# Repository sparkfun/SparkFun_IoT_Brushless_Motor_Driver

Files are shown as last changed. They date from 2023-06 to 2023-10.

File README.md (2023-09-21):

SparkFun IoT Brushless Motor Driver (ESP32 WROOM, TMC6300)
========================================

SparkFun IoT Brushless Motor Driver (ESP32 WROOM, TMC6300) (https://www.sparkfun.com/products/22132)

[*SparkFun IoT Brushless Motor Driver (ESP32 WROOM, TMC6300) (ROB-22132)*](https://www.sparkfun.com/products/22132)

The SparkFun IoT Brushless Motor Driver is an all-in-one development platform. It includes all the components to create a simple IoT device or learn about [control systems](https://en.wikipedia.org/wiki/Control_system). On the boaard, users will find an ESP32 microcontroller, a TMC6300 motor driver, a [gimbal motor](https://www.sparkfun.com/products/20441), a TMAG5273 hall-effect sensor, three INA240A1 inline current sensors, an MCP6021T low-side current sensor, two user buttons, a Qwiic connector, a 3-pin JST connector (for the gimbal motor), and a WS2812 RGB LED.

The TMC6300 from [ADI + Trinamic](https://www.trinamic.com/) is a powerful and easy-to-use three-phase motor driver with up to 2A (1.4A<sub>RMS</sub>) of total drive current. Separate high-side and low-side control of the three half-bridges allows for incredible control of each phase of the [motor commutation](https://fab.cba.mit.edu/classes/865.21/topics/power_electronics/commutation/#bldc-commutation). We've found the [*Arduino Simple Field Oriented Control*](https://docs.simplefoc.com/) library to work well with the TMC6300 motor driver.

However, a field-oriented control (FOC) algorithm requires some feedback to close and optimize the control loop. Therefore, we integrated a TMAG5273 hall-effect sensor and INA240A1 current sensor amplifiers *(both manufactured by [Texas Instruments](https://www.ti.com/))* into the design of the IoT motor driver board. This allows users to incorporate a [position sensor](https://docs.simplefoc.com/position_sensors) and [current sensing](https://docs.simplefoc.com/current_sense) into the FOC algorithm or any feedback control loop they choose to implement.

Repository Contents
-------------------

* **[/docs](/docs/)** - Online documentation files
    * [assets](/docs/assets/) - Assets files
        * [arduino_examples](/docs/assets/arduino_examples/) - Example code
        * [board_files](/docs/assets/board_files/) - Files for the product design
            * [Eagle design files](/docs/assets/board_files/eagle_files.zip) (.zip)
            * [Schematic](/docs/assets/board_files/schematic.pdf) (.pdf)
            * [Dimensions](/docs/assets/board_files/dimensions.pdf) (.pdf)
        * [component_documentation](/docs/assets/component_documentation/) - Datasheets for hardware components
        * [img/hookup_guide/](/docs/assets/img/hookup_guide/) - Images for hookup guide documentation
* **[/Hardware](/Hardware/)** - Eagle design files (.brd, .sch)
* **[/Production](/Production/)** - Production files

Documentation
--------------

* **[Hookup Guide (mkdocs)](http://docs.sparkfun.com/SparkFun_IoT_Brushless_Motor_Driver/)** - Hookup guide for the IoT Brushless Motor Driver hosted by GitHub pages.

*Need to download or print our hookup guide?*

* [Print *(Print to PDF)* from Single-Page View](http://docs.sparkfun.com/SparkFun_IoT_Brushless_Motor_Driver/print_view)

Product Variants
----------------

* [ROB-22132](https://www.sparkfun.com/products/22132)- v1.0, Initial Release

Version History
---------------

* [v10](https://github.com/sparkfun/SparkFun_IoT_Brushless_Motor_Driver/releases/tag/v10) - Initial Release

License Information
-------------------

This product is ***open source***!

Please review the [`LICENSE.md`](./LICENSE.md) file for license information.

If you have any questions or concerns about licensing, please contact technical support on our [SparkFun forums](https://forum.sparkfun.com/viewforum.php?f=152).

Distributed as-is; no warranty is given.

- Your friends at SparkFun.

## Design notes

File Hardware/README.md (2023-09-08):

SparkFun IoT Brushless Motor Driver Design Files
=====================================

The .sch and .brd files hare are Eagle CAD schematic and PCB design files from SparkFun Electronics.
A freeware version of Autodesk Eagle can be found [here](https://www.autodesk.com/products/eagle/free-download).

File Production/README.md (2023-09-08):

SparkFun IoT Brushless Motor Driver Production Files
=========================================

These are the production files SparkFun uses for printing PCBs.

License Information
-------------------
This product is open source! 

The hardware is released under [Creative Commons ShareAlike 4.0 International](https://creativecommons.org/licenses/by-sa/4.0/).

Please use, reuse, and modify these files as you see fit. Please maintain attribution to SparkFun Electronics and release anything derivative under the same license.

Distributed as-is; no warranty is given.

- Your friends at SparkFun.

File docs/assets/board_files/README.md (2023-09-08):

board_files directory
====================

1. A `dimensions*.pdf` file containing the board's measurements.
2. A `schematic.pdf` file containing the board's schematics.
3. An `eagle_files*.zip` folder containing the Eagle CAD schematics (`*.sch`) and PCB design (`*.brd`) files.
	* A freeware version of Autodesk Eagle can be found [here](https://www.autodesk.com/products/eagle/free-download).

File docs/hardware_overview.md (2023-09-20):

---
icon: material/cog
---

## Board Dimensions
The board dimensions are illustrated in the drawing below; the listed measurements are in inches.

<figure markdown>
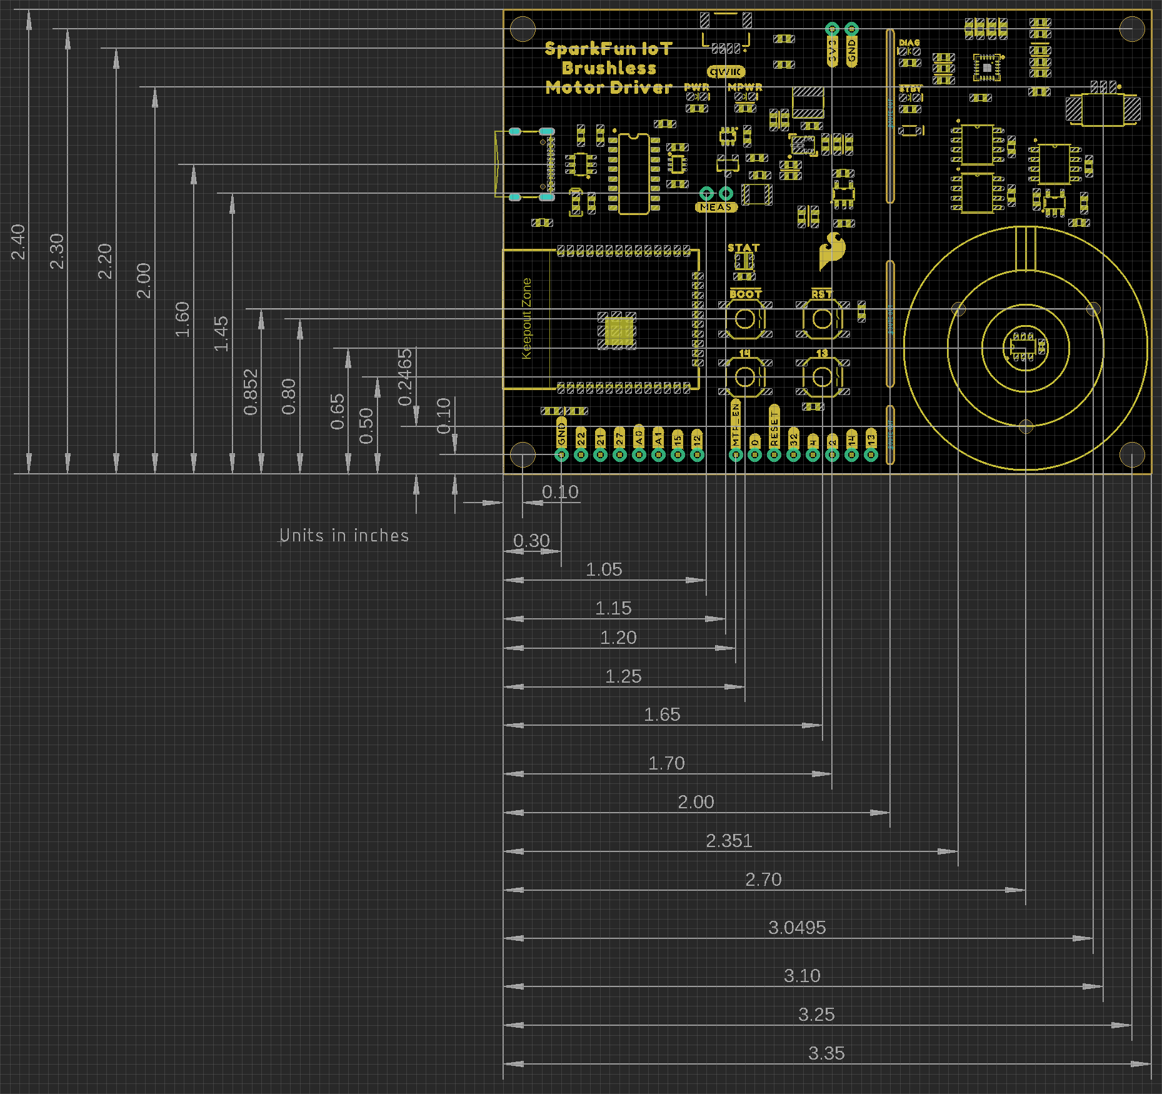
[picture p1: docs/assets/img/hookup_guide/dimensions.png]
Board Dimensions

<figcaption markdown>
[Board dimensions (PDF)](./assets/board_files/dimensions.pdf) for the IoT Motor Driver board, in inches.
</figcaption>
</figure>

??? tip "Need more measurements?"
	For more information about the board's dimensions, users can download the [eagle files](./assets/board_files/eagle_files.zip) for the board. These files can be opened in Eagle and additional measurements can be made with the dimensions tool.

	??? info ":octicons-download-16:{ .heart } Eagle - Free Download!"
		Eagle is a [CAD]("computer-aided design") program for electronics that is free to use for hobbyists and students. However, it does require an account registration to utilize the software.

		<center>
		[Download from<br>:autodesk-primary:{ .autodesk }](https://www.autodesk.com/products/eagle/free-download "Go to downloads page"){ .md-button .md-button--primary width="250px" }
		</center>
	
	??? info ":straight_ruler: Dimensions Tool"
		This video from Autodesk demonstrates how to utilize the dimensions tool in Eagle, to include additional measurements:

		<center>
		<div class="video">
		<iframe src="https://www.youtube.com/embed/dZLNd1FtNB8" title="EAGLE Dimension Tool" frameborder="0" allow="accelerometer; autoplay; clipboard-write; encrypted-media; gyroscope; picture-in-picture" allowfullscreen></iframe>
		</div>
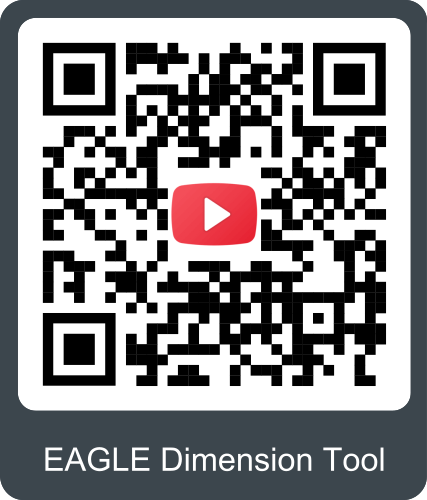
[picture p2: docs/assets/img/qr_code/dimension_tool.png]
QR code to play video
		
		</center>

## USB-C Connector
The USB connector is provided to power and program the board. For most users, it will be the primary programming interface for the ESP32 module on the IoT Motor Driver board.

<figure markdown>
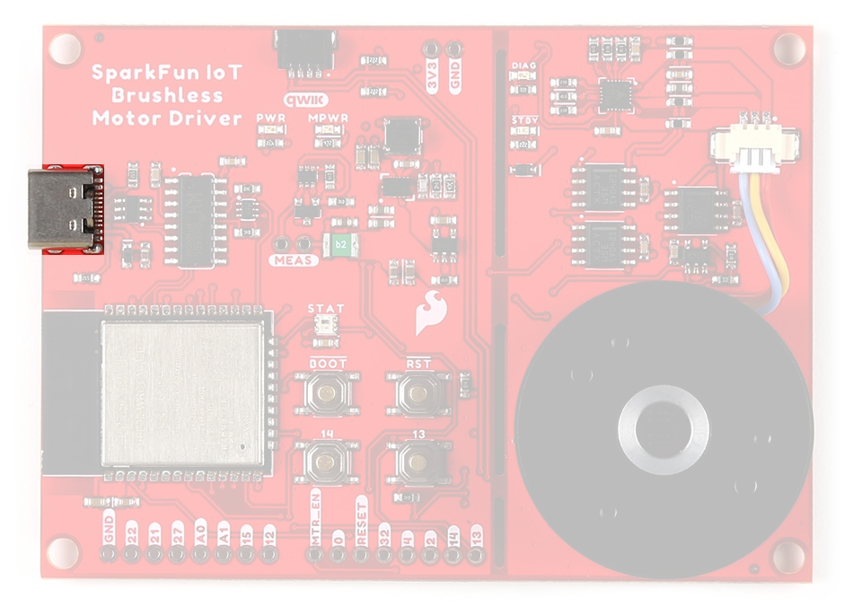
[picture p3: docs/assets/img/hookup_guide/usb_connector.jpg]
USB-C Connector

<figcaption markdown>USB-C connector on the IoT Motor Driver board.</figcaption>
</figure>

### Power
The IoT Motor Driver only requires **5V** to power all of the board's components. The simplest method to power the board is through the USB-C connector. Alternatively, the `3V3` pin can be used to supply power to any of the components, except the motor driver.

<figure markdown>
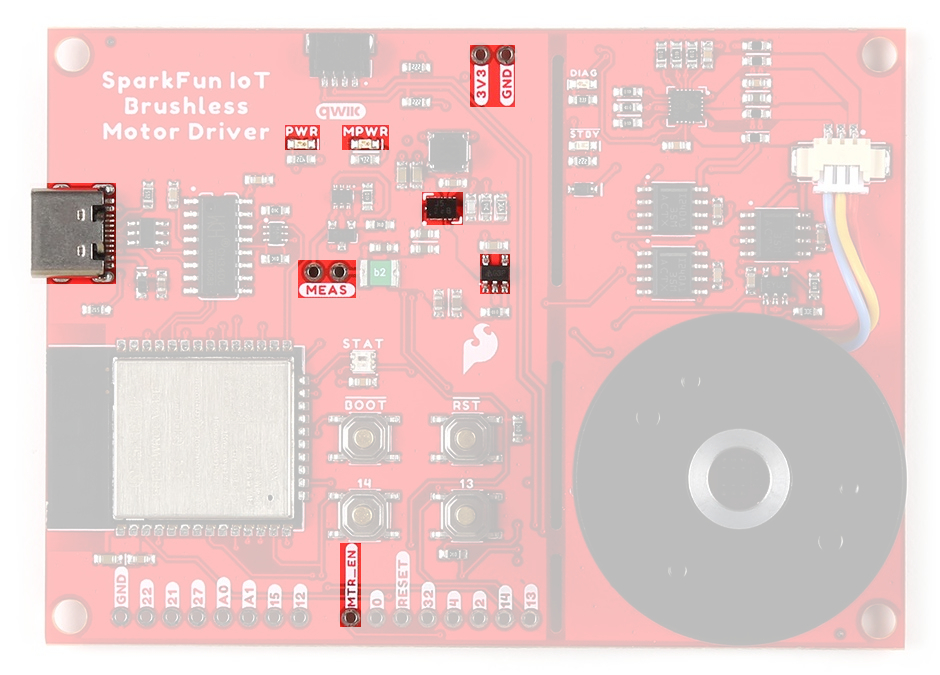
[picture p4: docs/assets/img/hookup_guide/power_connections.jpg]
Power connections

<figcaption markdown>IoT Motor Driver power connections.</figcaption>
</figure>

Below, is a general summary of the power circuitry on the board:

* **`3V3`** - Provides a regulated 3.3V from the USB (5V) power to the board, excluding the TMC6300 motor driver.
	* Used to power the ESP32-WROOM module, hall-effect and current sensors, CH340C Serial-to-UART bridge, Qwiic connector, and the WS2812 RGB LED.
	* The **3.3V** [AP2112](./assets/component_documentation/AP2112.pdf) LDO regulator can source up to 600mA.
	* Broken out as [PTH](https://en.wikipedia.org/wiki/Through-hole_technology "Plated Through Holes") pin.
* **`3V3_A`** - Provides a regulated 3.3V from the USB (5V) power to only the TMC6300 motor driver.
	* The motor driver will not function without power from the USB connector.
	* The **3.3V** [AP63357](./assets/component_documentation/AP63356-AP63357.pdf) LDO regulator can source up to 3.5A.
* **`VUSB`** - The voltage from the USB-C connector, usually **5V**.
	* Power source for the entire board.
		* Powers the two 3.3V voltage regulators (AP2112 and AP63357).
	* Features reverse current protection and a thermal fuse.
	* `MEAS` - These pins can be used to measure the current being drawn through the USB connector *(see the **[Jumpers](#jumpers)** section)*.
* **`GND`** - The common ground or the 0V reference for the voltage supplies.
* **Qwiic Connector** - Provides a regulated 3.3V voltage to the Qwiic devices.

!!! info
	For more details, users can reference the [schematic](./assets/board_files/schematic.pdf) and the datasheets of the individual components on the board.

??? warning "Motor Voltage"
	The [Gimbal Stabilizer Motor](https://cdn.sparkfun.com/assets/e/b/2/8/3/OT-EM3215_DC_Brushless_Gimbal_Motor_3_Phase_Datasheet.pdf) has an operating voltage range of 6 - 8V. However, we have found that it still functions properly with only 3.3V provided by the IoT Motor Driver board.

### CH340 Serial-to-UART
The CH340 allows the ESP32-WROOM to communicate with a computer/host device through the board's USB-C connection. This allows the board to show up as a device on the serial (or COM) port of the computer. Users will need to install the latest drivers for the computer to recognize the board *(see [**Software Overview**](/SparkFun_IoT_Brushless_Motor_Driver/software_overview/#ch340-driver) section)*.

## :fontawesome-solid-microchip:&nbsp;Microcontroller - ESP32-WROOM
The brains of the IoT Motor Driver, is an [ESP32-WROOM module](./assets/component_documentation/esp32-wroom-32e_datasheet_en.pdf) with 16MB of flash memory. Espressif's ESP32-WROOM module is a versatile, WiFi+BT+BLE MCU module that targets a wide variety of applications. At the core of this module is the ESP32-D0WDQ6 system on a chip (SoC) which is designed to be both scalable and adaptive microcontroller. Its laundry list of features include:

<div class="grid cards" markdown>

-	 Features:

	* Xtensa® Dual-Core 32-bit LX6 Microprocessor *(up to 240MHz)*
		* 448KB ROM and 520KB SRAM
		* 16MB of Embedded SPI Flash Storage
	* Cryptographic Hardware Accelerators
		* AES, SHA2, ECC, RSA-4096
	* Integrated 802.11 b/g/n WiFi 2.4GHz Transceiver *(up to 150Mbps)*
	* Integrated dual-mode Bluetooth (Bluetooth v4.2 and BLE)
	* 26 GPIO *(including strapping pins)*
		* 8x Capacitive Touch Electrodes
	* Operating Voltage: **3.0 to 3.6V**
		* WiFi: 380mA *(peak)*
		* Light-Sleep: 800&micro;A
		* Deep-Sleep: 10 - 150&micro;A

-	<figure markdown>
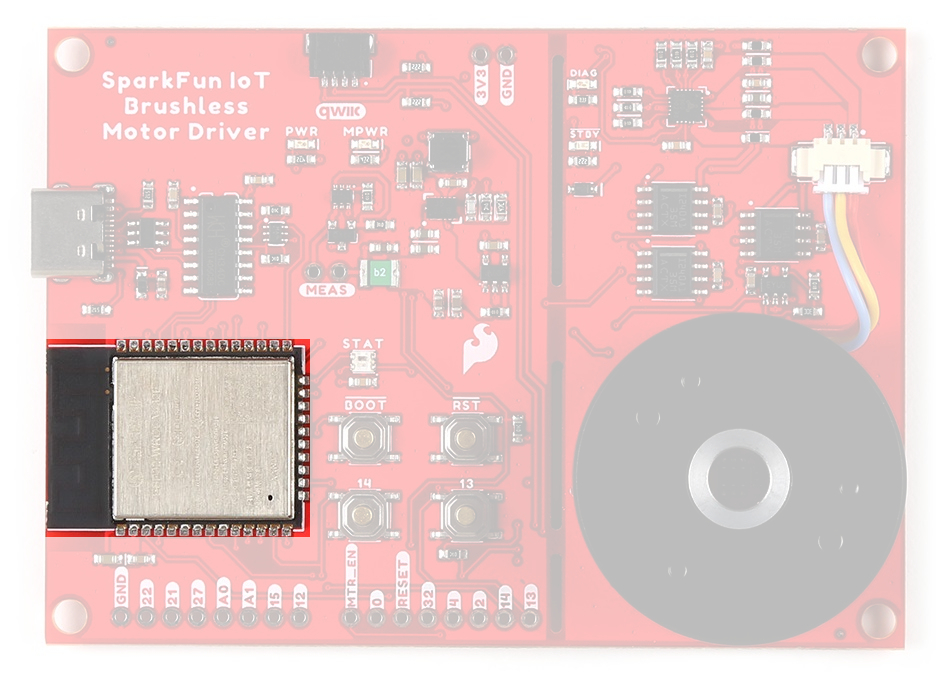
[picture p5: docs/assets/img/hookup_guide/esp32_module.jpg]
ESP32-WROOM
	
	<figcaption markdown>ESP32-WROOM module on the IoT Motor Driver.</figcaption>
	</figure>

</div>

!!! warning
	Users should be aware of the following nuances and details of this board

	* The ESP32-WROOM is only compatible with **2.4GHz WiFi** networks; it will not work on the 5GHz bands.
	* For details on the boot mode configuration, please refer to [section **3.3 Strapping Pins**](./assets/component_documentation/esp32-wroom-32e_datasheet_en.pdf#8) of the ESP32-WROOM module datasheet.

!!! info
	The ESP32-WROOM module has various power modes:

	* **Active** - The chip radio is powered on. The chip can receive, transmit, or listen.
	* **Modem Sleep** - The CPU is operational and the clock is configurable. The Wi-Fi/Bluetooth
	baseband and radio are disabled.
	* **Light Sleep** - The CPU is paused. The RTC memory and RTC peripherals, as well as the ULP
	coprocessor are running.
	* **Deep Sleep** - Only the RTC memory and RTC peripherals are powered on. The ULP coprocessor is functional.
	* **Hibernation** - Only one RTC timer on the slow clock and certain RTC GPIOs are
	active.
	* **Off** - Chip is powered off
	
	*For more information on the power management of the ESP32-WROOM module, pleaser refer to **Section 3.7** and **Tables: 8 and 17** of the [ESP32 SoC Datasheet](./assets/component_documentation/esp32_soc_datasheet_en.pdf).*

### Debugging
For users interested in debugging their code, the [JTAG pins](https://docs.espressif.com/projects/esp-idf/en/latest/esp32/api-guides/jtag-debugging/configure-other-jtag.html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) are broken out on the board. However, the debugging feature is only available through the [ESP-IDF](https://docs.espressif.com/projects/esp-idf/en/latest/esp32/api-guides/jtag-debugging/index.html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).

* **`TMS`**: `GPIO 14`
* **`TDI`**: `GPIO 12`
* **`TCK`**: `GPIO 13`
* **`TDO`**: `GPIO 15`

<figure markdown>
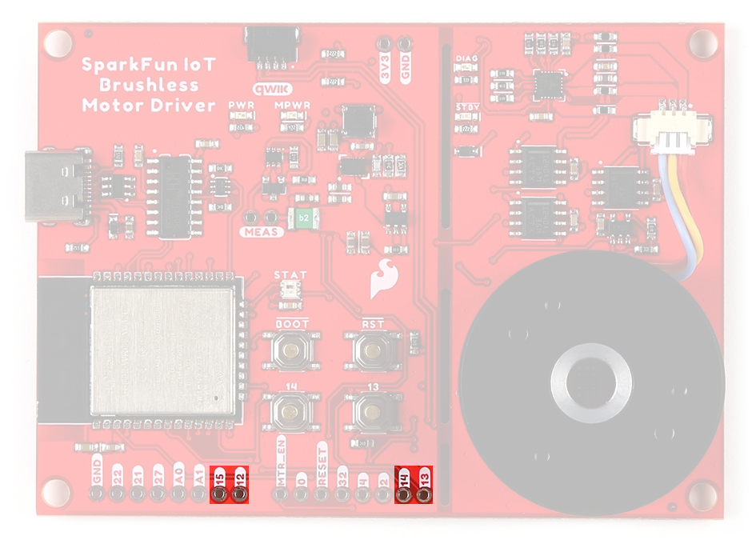
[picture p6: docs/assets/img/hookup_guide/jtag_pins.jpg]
JTAG Pins

<figcaption markdown>The JTAG pins of the ESP32-WROOM module on the IoT Motor Driver.</figcaption>
</figure>

### Firmware Download Mode
Users can manually force the board into the [serial bootloader](https://docs.espressif.com/projects/esptool/en/latest/esp32/advanced-topics/boot-mode-selection.html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) with the ++"BOOT"++ button. Please, refer to the [**Boot Button** section](#boot-button) below for more information.

### Peripherals and I/O
!!! warning
	Users should be aware of the following nuances of this board

	* &#9889; All the GPIO on the IoT Motor Driver are **3.3V** pins.
		* The I/O pins are <strong>not 5V-tolerant</strong>! To interface with higher voltage components, a **[logic level adapter](https://learn.sparkfun.com/tutorials/bi-directional-logic-level-converter-hookup-guide)** is recommended.
	* &#9889; There are electrical limitations to the amount of current that the ESP32-WROOM module can sink or source. For more details, check out the [ESP32-WROOM module datasheet](./assets/component_documentation/esp32-wroom-32e_datasheet_en.pdf).
	* There are some limitations to the ADC performance, see the <b>Note</b> from the [**ADC Characteristics** section of the ESP32 SoC datasheet](./assets/component_documentation/esp32_soc_datasheet_en.pdf).

The ESP32-WROOM module has *26 multifunctional GPIO*, of which, **16 I/O pins** are used to interface with motor driver, sensors, and status LED on the board. Additionally, **13 I/O pins** are broken out to [PTH](https://en.wikipedia.org/wiki/Through-hole_technology "Plated Through Holes") pins and the users buttons. All of the [IoT Motor Driver](https://www.sparkfun.com/products/22132) pins have a .1" pitch spacing for headers.

While all of the GPIO pins are capable of functioning as digital I/O pins, various pins can have additional capabilities with the [pin multiplexing](https://docs.espressif.com/projects/arduino-esp32/en/latest/tutorials/io_mux.html?#id1) feature of the ESP32 SoC. For more technical specifications on the **I/O** pins, please refer to the [ESP32 SoC datasheet](./assets/component_documentation/esp32_soc_datasheet_en.pdf).

* 13x 12-bit analog to digital converter (ADC) channels
* 3x UARTs (only two are configured by default in the Arduino IDE, one UART is used for bootloading/debug)
* 3x SPI (only one is configured by default in the Arduino IDE)
* 2x I<sup>2</sup>C (only one is configured by default in the Arduino IDE)
* 2x I<sup>2</sup>S Audio
* 2x digital-to-analog converter (DAC) channels
* 16x 20-bit PWM outputs
* 8x Capacitive Touch Inputs

!!! info
	Users should be aware of the following limitations for the board in the Arduino IDE.

	* Not all of the features, listed above, are available in the Arduino IDE. For the full capabilities of the ESP32, the Espressif IDF should be utilized.
		* Only one I<sup>2</sup>C bus is defined.
		* Only two UART interfaces are available.
			* **UART (USB):** `Serial`
			* **`RX`/`TX` Pins:** `Serial1`
		* Only one SPI bus is defined.

#### Peripheral Devices
This development board features several components operating together to create an IoT device. Their connections are shown in the diagram below and their operations are listed in the boxes below. *For more details on each component, please refer to the sections below.*

<figure markdown>
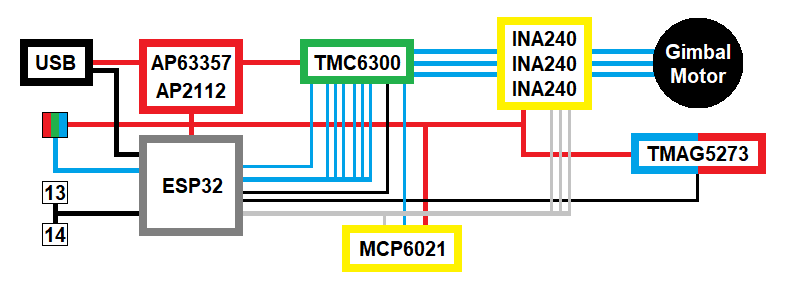
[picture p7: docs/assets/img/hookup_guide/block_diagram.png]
Block Diagram

<figcaption markdown>Block diagram of the IoT Motor Driver board's peripherals.</figcaption>
</figure>

<div class="grid cards col-2" markdown>

-   **Inputs**

	---

	* TMC6300 Motor Driver
		* Diagnostic Pin
	* TMAG5273 Hall-Effect Sensor
	* INA240 Current-Sense Amplifier
	* MCP6021 Operational Amplifier
	* User Buttons

-   **Outputs**

	---

	* TMC6300 Motor Driver
		* Half-Bridge Pins
		* Standby Pin
	* RGB Status LED

</div>

#### Pin Functionality
There are several pins that have special functionality in addition to general **digital I/O**. These pins and their additional functions are listed in the tabs below. For more technical specifications on the **I/O** pins, you can refer to the [schematic](./assets/board_files/schematic.pdf), [ESP32-WROOM module datasheet](./assets/component_documentation/esp32-wroom-32e_datasheet_en.pdf), [ESP32 SoC datasheet](./assets/component_documentation/esp32_soc_datasheet_en.pdf), and [documentation for the ESP32 Arduino core](https://docs.espressif.com/projects/arduino-esp32/en/latest/tutorials/io_mux.html?#peripherals).

=== "Digital I/O Pins"
	Any GPIO pin on the ESP32-WROOM module can function as a digital I/O *(input or output)*. However, users will need to declare the [**`pinMode()`** *(link)*](https://www.arduino.cc/reference/en/language/functions/digital-io/pinmode/) in the setup of their <b>sketch</b> (programs written in the Arduino IDE) to configure a pin as an input or an output.

	<div class="grid cards col-2" markdown>

	-   **Inputs**

		---

		When configured properly, an <b>input</b> pin will be looking for a <b>HIGH</b> or <b>LOW</b> state. <b>Input</b> pins are <b>High Impedance</b> and takes very little current to move the input pin from one state to another.

		<center>

		| **`DIAG` *(TMC6300)*** | `GPIO 34` |
		| :--------------------- | :-------- |
		| **`INT` *(TMAG5273)*** | `GPIO 04` |
		| **Button ++"13"++**    | `GPIO 13` |
		| **Button ++"14"++**    | `GPIO 14` |

		</center>

	-   **Outputs**

		---

		When configured as an <b>output</b> the pin will be at a <b>HIGH</b> or <b>LOW</b> voltage. <b>Output</b> pins are <b>Low Impedance</b>: This means that they can provide a relatively substantial amount of current to other circuits.

		<center>

		| **`VIO` *(TMC6300)*** | `GPIO 05` |
		| :-------------------- | :-------- |
		| **WS2812**            | `GPIO 02` |

		</center>

		!!! warning
			**&#9889;** There are electrical limitations to the amount of current that the ESP32-WROOM module can sink or source. For more details, check out the <a href="./assets/component_documentation/esp32-wroom-32e_datasheet_en.pdf">ESP32-WROOM module datasheet</a>.

	</div>

	!!! tip
		Pins cannot be configured to operate simultaneously as an input and output, without implementing the pin as an interrupt.

=== "Analog Inputs"
	The ESP32-WROOM module provides a <b>12-bit ADC</b> input on thirteen of its I/O pins. This functionality is accessed in the Arduino IDE using the <a href="https://www.arduino.cc/reference/en/language/functions/analog-io/analogread/">`analogRead(pin)` function</a>. *(The available ADC pins are highlighted in the image below.)*

	<center>

	| **Current Sensor** | INA240 *(`U`)* | INA240 *(`V`)* | INA240 *(`W`)* | MCP6021   |
	| :----------------- | :------------: | :------------: | :------------: | :-------: |
	| **Analog Input**   | `GPIO 35`      | `GPIO 36`      | `GPIO 39`      | `GPIO 32` |
	
	</center>

	!!! info
		By default, in the Arduino IDE, `analogRead()` returns a 10-bit value. To change the resolution of the value returned by the `analogRead()` function, use the [`analogReadResolution(bits)` function](https://www.arduino.cc/reference/en/language/functions/zero-due-mkr-family/analogreadresolution/).
	
	!!! tip
		To learn more about analog vs. digital signals, check out this great [tutorial](https://learn.sparkfun.com/tutorials/analog-vs-digital).

		<div class="grid cards col-4" markdown  align="center">

		-   <a href="https://learn.sparkfun.com/tutorials/89">
			<figure markdown>
			Tutorial thumbnail
			</figure>

			---
			
			**Analog vs. Digital**</a>

		</div>

=== "PWM & Analog (DAC) Outputs"
	The ESP32-WROOM module supports up to sixteen channels of <b>20-bit PWM</b> (Pulse Width Modulation) outputs on any of its I/O pins. This is accessed in the Arduino IDE using the [`analogWrite(pin, value)` function](https://www.arduino.cc/reference/en/language/functions/analog-io/analogwrite/). *(Any I/O pin can be used for the PWM outputs; the available DAC pins, with true analog outputs, are highlighted in the image below.)*

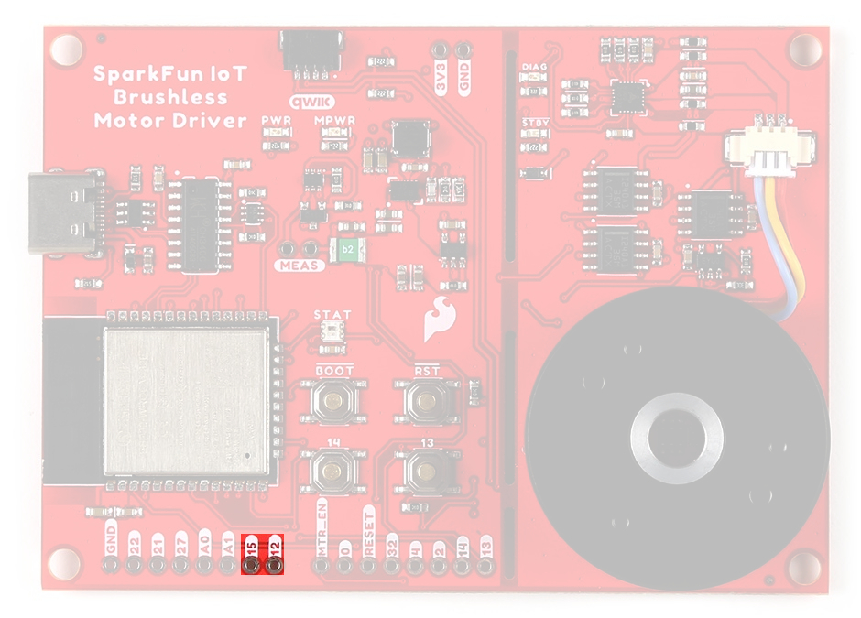
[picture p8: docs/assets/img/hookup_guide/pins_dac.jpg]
Annotated image of DAC pins
	

	<center>

	| **Motor Driver** | `UH`      | `UL`      | `VH`      | `VL`      | `WH`      | `WL`      |
	| :--------------- | :-------: | :-------: | :-------: | :-------: | :-------: | :-------: |
	| **PWM Output**   | `GPIO 16` | `GPIO 17` | `GPIO 18` | `GPIO 23` | `GPIO 19` | `GPIO 33` |

	</center>

	!!! info
		By default, in the Arduino IDE, `analogWrite()` accepts an 8-bit value. To change the resolution of the PWM signal for the `analogWrite()` function, use the [`analogWriteResolution(bits)` function](https://www.arduino.cc/reference/en/language/functions/zero-due-mkr-family/analogwriteresolution/). *(The PWM output is not a true analog signal.)*
	
	!!! tip
		To learn more about pulse width modulation (PWM), check out this great [tutorial](https://learn.sparkfun.com/tutorials/pulse-width-modulation).

		<div class="grid cards col-4" markdown  align="center">

		-   <a href="https://learn.sparkfun.com/tutorials/51">
			<figure markdown>
			Tutorial thumbnail
			</figure>

			---
			
			**Pulse Width Modulation**</a>

		</div>

=== "Serial Pins"
	The ESP32-WROOM module provides three UART ports. By default, the UART port for the USB connection (`Serial`) and the labeled UART I/O pins on the board (`Serial1`) can be accessed through the Arduino IDE using the [serial communication class](https://www.arduino.cc/reference/en/language/functions/communication/serial/).

	!!! info
		By default, in the Arduino IDE, the **<Dev Board Name>** board definition supports:		

		* `Serial` - **UART (USB)**
		* `Serial1` - **Pins: `RX`/`TX` (`GPIO 16`/`GPIO 17`)**

		??? note
			* The `GPIO 16` and `GPIO 17` pins of `Serial1` are already dedicated to the `UH`/`UL` half-bridge on the TMC63000 motor driver and are not broken out for users to access.
			* In order to utilize the serial communication on the strapping pins, users will need to create a custom serial port object and declare which pins to access.

	!!! tip
		To learn more about serial communication, check out this great [tutorial](https://learn.sparkfun.com/tutorials/serial-communication).

		<div class="grid cards col-4" markdown  align="center">

		-   <a href="https://learn.sparkfun.com/tutorials/8">
			<figure markdown>
			Tutorial thumbnail
			</figure>

			---
			
			**Serial Communication**</a>

		</div>

	!!! tip
		We have noticed that with the ESP32 Arduino core, `Serial.available()` does not operate instantaneously. This is due to an interrupt triggered by the UART, to empty the FIFO when the <b>`RX`</b> pin is inactive for two byte periods:

		* At 9600 baud, `hwAvailable` takes [`number of bytes received` + 2] x 1 ms = <b>11 ms</b> before the UART indicates that data was received from: `\r\nERROR\r\n`.
		* At 115200 baud, `hwAvailable` takes [`number of bytes received` + 2] x .087 ms = <b>~1 ms</b> before the UART indicates that data was received from: `\r\nERROR\r\n`.

		*For more information, please refer to this [chatroom discussion](https://gitter.im/espressif/arduino-esp32?at=5e25d6370a1cf54144909c85).*

=== "SPI Pins"
	The ESP32-WROOM module provides three SPI buses. By default, in the Arduino IDE, the [SPI class](https://www.arduino.cc/en/reference/SPI) is configured to utilize pins `GPIO 18` *(SCK)*, `GPIO 19` *(POCI)*, `GPIO 23` *(PICO)*. In order to utilize the other SPI ports or objects, users will need to create a custom SPI object and declare which pins to access.
	
	!!! info
		To comply with the latest [OSHW](https://www.oshwa.org/) design practices, we have [adopted the new SPI signal nomenclature](https://www.sparkfun.com/spi_signal_names) (**SDO**/**SDI** and **PICO**/**POCI**). The terms Master and Slave are now referred to as Controller and Peripheral. The `MOSI` signal on a controller has been replaced with `SDO` or `PICO`. Please refer to this [announcement on the decision to deprecate the **MOSI**/**MISO** terminology and transition to the **SDO**/**SDI** naming convention](https://www.oshwa.org/a-resolution-to-redefine-spi-signal-names).
	
	<center>

	| **SCK**             | `GPIO 18` (`SCK`)  |
	| :------------------ | :----------------- |
	| **SDI** or **POCI** | `GPIO 19` (`MISO`) |
	| **SDO** or **PICO** | `GPIO 23` (`MOSI`) |
	| **CS**              | `GPIO 5` (`SS`)    |

	</center>

	??? note
		* The `GPIO 18`,`GPIO 19`, and `GPIO 23` pins of the `SPI` bus are already dedicated to the `VH`/`WH`/`VL` MOSFETs on the TMC63000 motor driver and are not broken out for users to access.
		* The `CS` pin associated with `GPIO 05` is also already dedicated to the `STBY` pin of the TMC63000 motor driver and is not broken out for users to access.
	
	!!! tip
		To learn more about the serial peripheral interface (SPI) protocol, check out this great [tutorial](https://learn.sparkfun.com/tutorials/serial-peripheral-interface-spi).

		<div class="grid cards col-4" markdown  align="center">

		-   <a href="https://learn.sparkfun.com/tutorials/16">
			<figure markdown>
			Tutorial thumbnail
			</figure>

			---
			
			**Serial Peripheral Interface (SPI)**</a>

		</div>

=== "I<sup>2</sup>C Pins"
	The ESP32-WROOM module module can support up to two I<sup>2</sup>C buses. By default, in the Arduino IDE, the [Wire class](https://www.arduino.cc/en/reference/wire) is configured to utilize pins `GPIO 21` *(SDA)* and `GPIO 22` *(SCL)*. These pins share the same I<sup>2</sup>C bus with the Qwiic connector and TMAG5273 hall-effect sensor. In order to utilize the other I<sup>2</sup>C ports, users will need to create a custom Wire object and declare which pins to access.
	
	<div class="grid cards col-2" markdown>

	-   <center>

		**I<sup>2</sup>C Pins**

		| **SCL** | `GPIO 22` |
		| :------ | :-------- |
		| **SDA** | `GPIO 21` |

		</center>

		---

		TMAG5273 I<sup>2</sup>C Address:

		* **0x35 *(Default)*** (7-bit)
		* 0x6A (write)/0x6B (read)

	-   <figure markdown>
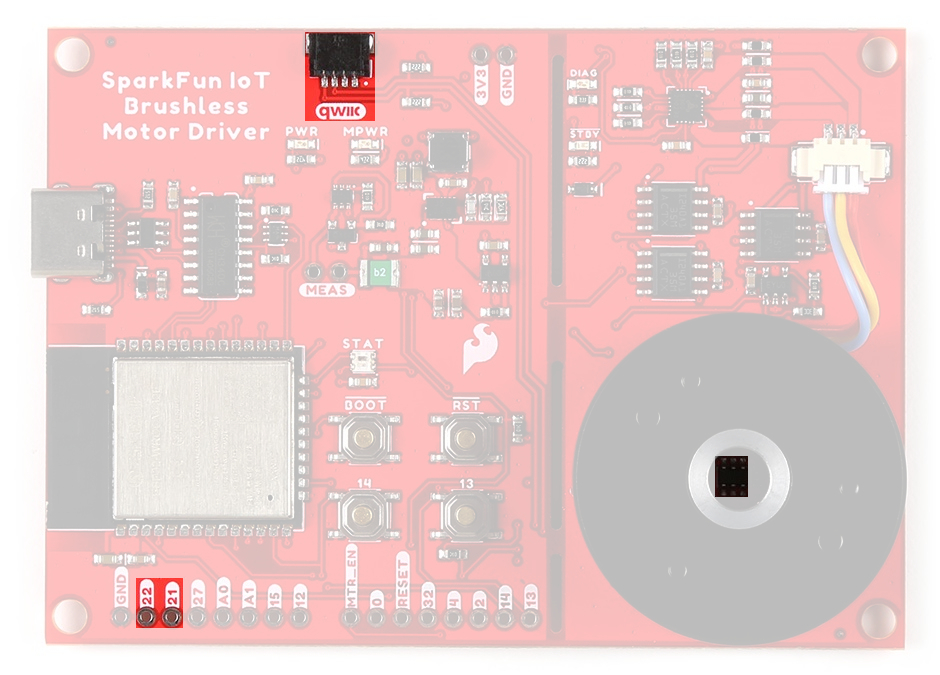
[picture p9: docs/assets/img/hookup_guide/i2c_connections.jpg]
		
		<figcaption markdown>Default I<sup>2</sup>C bus connections for the IoT Motor Driver.</figcaption>
		</figure>

	</div>

	!!! tip
		To learn more about the inter-integrated circuit (I<sup>2</sup>C) protocol, check out this great [tutorial](https://learn.sparkfun.com/tutorials/i2c).

		<div class="grid cards col-4" markdown  align="center">

		-   <a href="https://learn.sparkfun.com/tutorials/82">
			<figure markdown>
			Tutorial thumbnail
			</figure>

			---
			
			**Inter-Integrated Circuit (I<sup>2</sup>C)**</a>

		</div>

## :fontawesome-solid-microchip:&nbsp;Motor Driver - TMC6300

The [TMC6300](./assets/component_documentation/TMC6300.pdf) from [Trinamic Motion Control](https://www.trinamic.com/), part of Analog Devices, is a low voltage, 3-Phase [BLDC](https://en.wikipedia.org/wiki/Brushless_DC_electric_motor "Brushless DC")/[PMSM](https://en.wikipedia.org/wiki/Synchronous_motor#Permanent-magnet "Permanent-Magnet Synchronous Motor") motor driver utilizing separate high-side and low-side control signals for its three half-bridges.

<div class="grid cards" markdown>

-	 Features:

	* VIN: 2.0V to 11.0V
		* Operating current: 7mA
		* Standby current: 30nA
	* VOUT: 1.8V
	* 3 Half-Bridges
		* 3 High-side MOSFETs
		* 3 Low-side MOSFETs
	* I/O Supply Voltage Input
	* Diagnostic Output
	* Overtemperature Protection
		* Shutdown Temperature: 150&deg;C
		* Typical Power Dissipation: 1W
	* Short Protection

	!!! info
		For more details, please refer to the [TMC6300 datasheet](./assets/component_documentation/TMC6300.pdf).

-	<figure markdown>
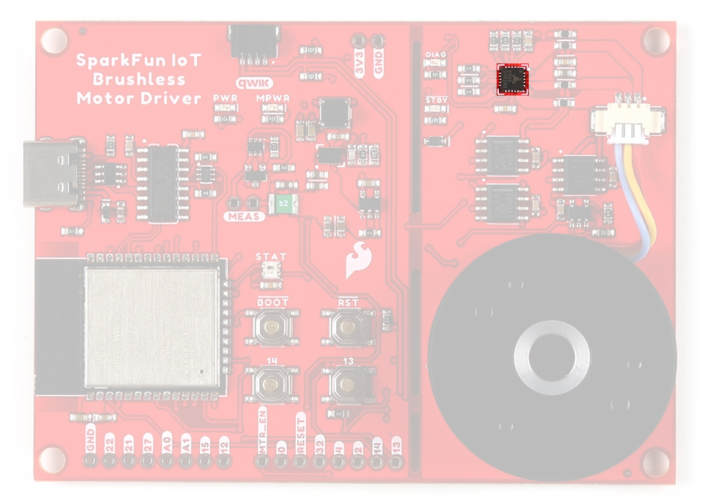
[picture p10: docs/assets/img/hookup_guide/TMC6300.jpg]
	
	<figcaption markdown>TMC6300 chip on the IoT Motor Driver.</figcaption>
	</figure>

	For users unfamiliar with the TMC6300 motor driver, please check out our hookup guide below.

	<article class="grid cards col-4" markdown  align="center">

	-   <a href="http://docs.sparkfun.com/SparkFun_Three_Phase_Motor_Driver-TMC6300/">
		<figure markdown>
		Tutorial thumbnail
		</figure>

		---
		
		**TMC6300 BLDC Motor Driver Hookup Guide**</a>

	</article>

</div>

### Half-Bridges

The TMC6300 features high-side and low-side MOSFET pairs of the three available half-bridges which control the commutation of the three motor phases.

<figure markdown>
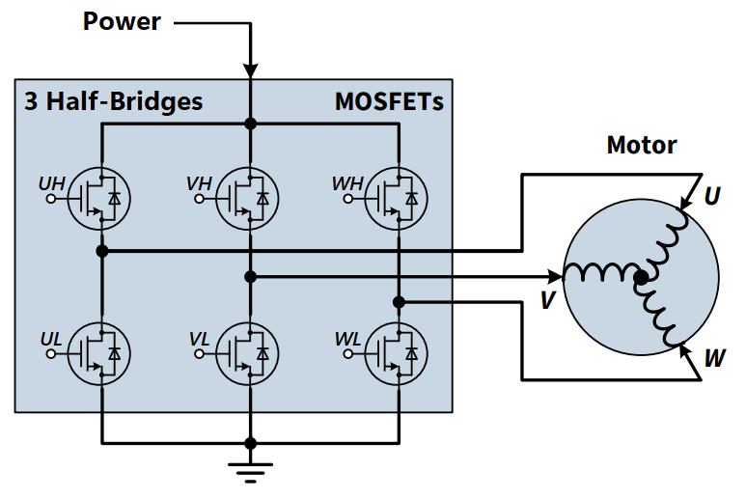
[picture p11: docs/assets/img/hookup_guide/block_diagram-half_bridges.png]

<figcaption markdown>
6 PWM control of a 3-phase motor commutation.<br>
(Source: Modified from the [Block commutation vs. FOC in power tool motor control](https://www.infineon.com/dgdl/Infineon-Motor_power_tool_Block_Commutation_vs_FOC-ApplicationNotes-v01_00-EN.pdf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) application note)
</figcaption>
</figure>

=== "Input"
	The electronic commutation sequence for these MOSFETs will depend on the motor that is connected. For most cases, users will provide a PWM signal to each of these pins. *These are active-high pins.*

	<center>

	| ESP32-WROOM  | `16` | `17` | `18` | `23` | `19` | `33` |
	| :----------- | :--: | :--: | :--: | :--: | :--: | :--: |
	| Motor Driver | `UH` | `UL` | `VH` | `VL` | `WH` | `WL` |

	</center>

	??? info "Active High"
		By pulling the pin high, the MOSFET will enable power to flow through that section of the half-bridge.

=== "Output"
	With the electronic commutation sequence provided to the half-bridges, the output motor phases will drive a connected motor.

	<figure markdown>
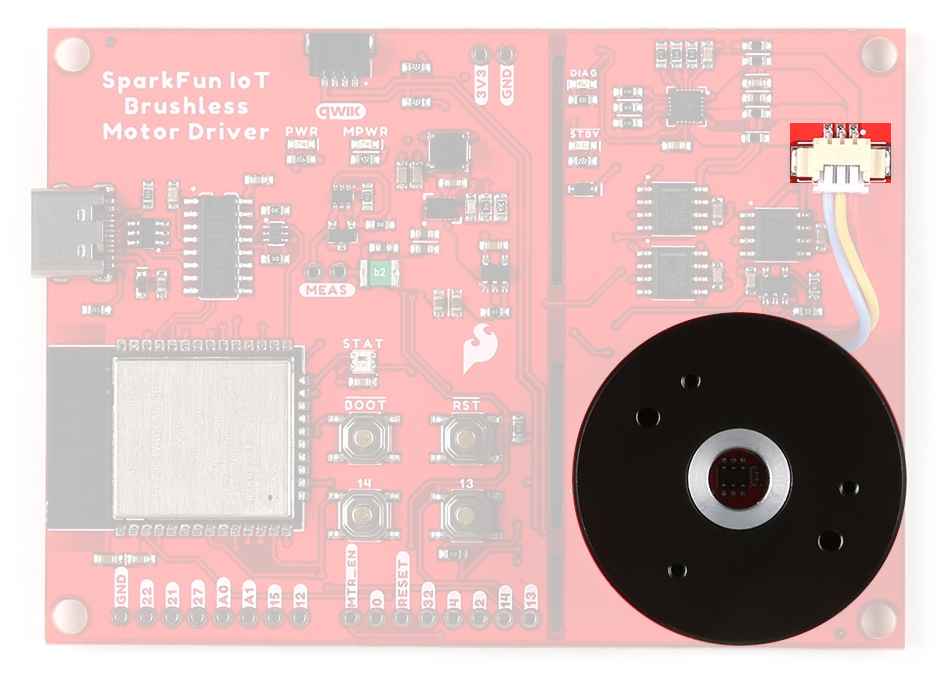
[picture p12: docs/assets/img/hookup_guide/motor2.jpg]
	
	<figcaption markdown>
	The three motor phase outputs (`U`/`V`/`W`) from the TMC6300 are used to drive the gimbal motor, attached through the JST connector.
	</figcaption>
	</figure>

#### Motor Commutation

The TMC6300 relies on an electrical [commutation](https://fab.cba.mit.edu/classes/865.21/topics/power_electronics/commutation/#bldc-commutation) sequence/signal to drive the motor phases to a [BLDC](https://en.wikipedia.org/wiki/Brushless_DC_electric_motor "brushless DC") or [PMSM](https://en.wikipedia.org/wiki/Synchronous_motor#Permanent-magnet "permanent magnet synchronous motor") motor. The commutation signals for these motors are trapezoidal for BLDC motors and sinusoidal for PMSM motors.

<div class="grid cards" markdown>

-	<figure markdown>
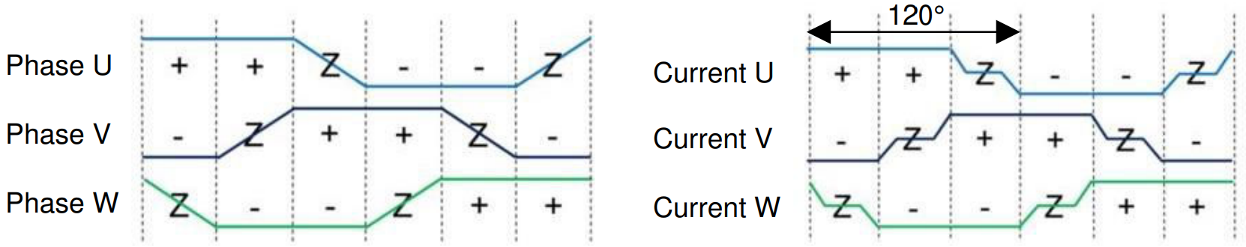
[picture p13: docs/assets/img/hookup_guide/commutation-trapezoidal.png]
	
	<figcaption markdown>
	Trapezoidal motor commutation.
	</figcaption>
	</figure>

-	<figure markdown>
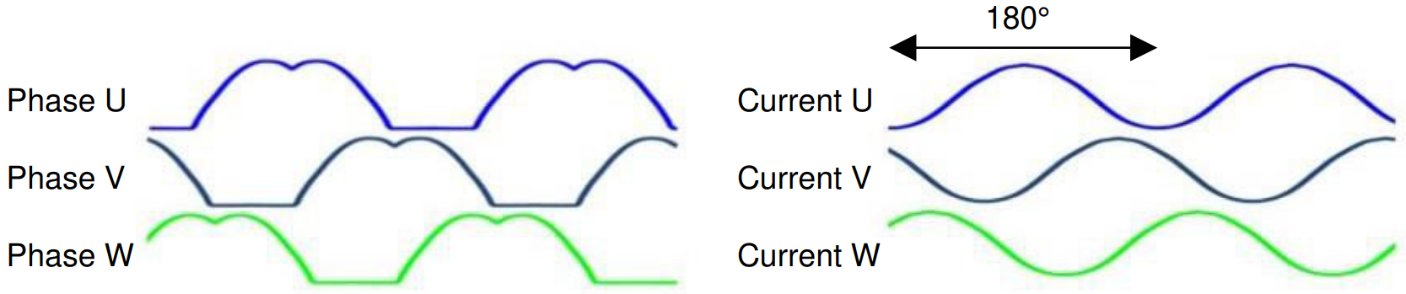
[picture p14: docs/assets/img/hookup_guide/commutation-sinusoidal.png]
	
	<figcaption markdown>
	Sinusoidal motor commutation.
	</figcaption>
	</figure>

</div>

<center>
*(Source: [Brushless-DC Motor Driver Considerations and Selection Guide](https://www.ti.com/lit/an/slvaes1a/slvaes1a.pdf) application note)*
</center>

!!! tip "Gimbal Motor"
	Based on measuring the output from one of the coils, our gimbal motor is a PMSM and would require a sinusoidal waveform to drive the motor. It should be noted that a trapezodial waveform can probably be used; however, users may notice effects such as cogging.

	<figure markdown>
	
	<figcaption markdown>
	Sinusoidal PWM signal.<br>
	(Source: [Demystifying BLDC motor commutation: Trap, Sine, & FOC](https://www.ti.com/lit/ml/slyp711/slyp711.pdf))
	</figcaption>
	</figure>

	For a trapezoidal signal, the high-side (HS) and low-side (LS) MOSFETs, can just be driven high or low. However, in order to approximate a sinusoidal signal, a progressively varying PWM signal must be provided with all six signals in sync with each other.

### `VIO`/Standby Pin

In it's default configuration, the `VIO` pin is used to enable the motor driver and set the logic level voltage of the TMC6300 inputs. However, the `VIO` pin also operates as a standby pin when it is pulled `LOW`. In standby, the TMC6300 resets and sits in standby mode.

Users can control the `VIO` pin with `GPIO 05` on the ESP32-WROOM module, to reset the TMC6300 or put it in standby mode.

### Diagnostic Pin

The diagnostic pin is triggered based on different faults *(i.e. shorts and overtemperature)* detected by the IC. By default, the status will be indicated by the, green diagnostic, `DIAG` LED and will remail `LOW` until triggered. Once triggered, users will need to disable and reset the TMC6300 or power cycle the board.

Users can monitor the diagnostic pin with `GPIO 34` on the ESP32-WROOM module, to determine if the TMC6300 need to be reset to clear a fault.

### Current Sense Pin
The current sense pin is the foot point of the `U` and `V` half-bridges, with a 0.12&ohm; resistor attached. Users can measure the voltage across the resistor to determine the current flowing to the motor *(see the **[Low-side Op Amp - MCP6021](#low-side-op-amp-mcp6021)** section below)*.

## :fontawesome-solid-microchip:&nbsp;Hall-Effect Sensor - TMAG5273
The [TMAG5273](./assets/component_documentation/TMAG5273.pdf) from [Texas Instruments](https://www.ti.com/), is a 3-axis hall-effect sensor utilizing a 12-bit ADC. For more information, please refer to the [TMAG5273 datasheet](./assets/component_documentation/TMAG5273.pdf).

<div class="grid cards col-4" markdown>

-   Features:

	* I<sup>2</sup>C Address:
		* **0x35 *(Default)*** (7-bit)
		* 0x6A (write)/0x6B (read)
	* Magnetic Range *(Sensitivity)*:
		* &PlusMinus; 40mT *(820 LSB/mT)*
		* &PlusMinus; 80mT *(410 LSB/mT)*
	* Magnetic Drift: 5%
	* Rotational Accuracy: &PlusMinus; 0.5&deg;/360&deg; rotation
	* Voltage Range: **1.7 - 3.6V**
		* Sleep: 5nA
		* Wake-Up/Sleep: 1µA
		* Active: 2.3mA
	* Operating Temperature: –40 - 125&deg;C
	* Integrated temperature compensation
	* Configurable sample rate

-   <figure markdown>
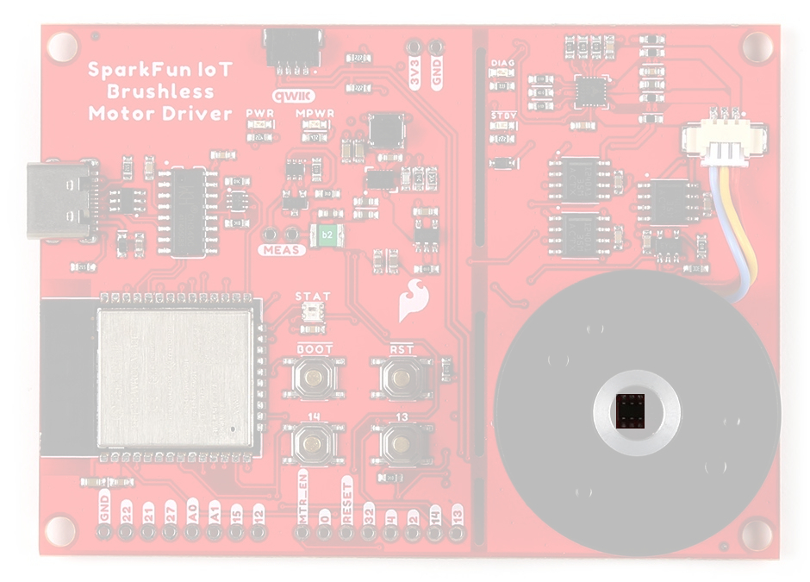
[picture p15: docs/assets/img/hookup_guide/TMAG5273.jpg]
	
	<figcaption markdown>The TMAG5273 hall-effect sensor on the IoT Motor Driver.</figcaption>
	</figure>

	!!! tip "Magnetic Axes"
		On the IoT Motor Driver, users will primarily be interested in magnetic field of the X-Y axes to measure the position of the gimbal motor.

		<figure markdown>
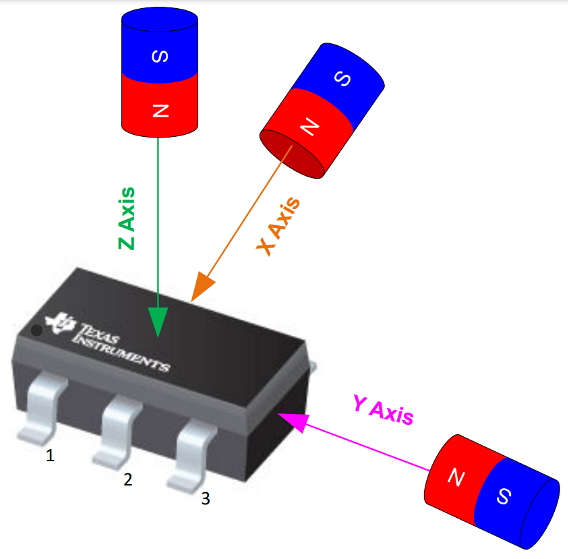
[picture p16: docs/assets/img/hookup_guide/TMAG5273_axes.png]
Magnetic axes
		
		<figcaption markdown>The magnetic axes of TMAG5273 hall-effect sensor.</figcaption>
		</figure>

</div>

!!! info
	For more details, please refer to the [TMAG5273 datasheet](./assets/component_documentation/TMAG5273.pdf).

### Interrupt Pin

The interrupt pin of the TMAG5723 can be configured in different modes to utilize either the `INT` or `SCL` pins.

* No interrupt
* Interrupt through `INT`
* Interrupt through `INT` except when I2C busy
* Interrupt through `SCL`
* Interrupt through `SCL` except when I2C busy

!!! tip
	We recommend utilizing the default `INT` pin to trigger interrupts; as it is already connected to `GPIO 04` of the ESP32-WROOM module.

	??? warning "Bus Contention"
		Texas Instruments does not recommend sharing the I<sup>2</sup>C bus with multiple devices when using the `SCL` pin for the interrupt function. The `SCL` interrupt can potentially corrupt the transactions with other devices, when present on the same I<sup>2</sup>C bus.

!!! note
	The TMAG5273 is programmed to detect a magnetic threshold in wake-up or sleep mode. Once the magnetic threshold cross is detected, the device asserts a latched interrupt signal through the INT pin, and goes back to stand-by mode. The interrupt latch is cleared through the `SCL` pin.

## Current Sensors
There are two different types of Op Amps on the board to amplify the input voltage for the current measurements.

* The INA240 is used for the in-line current measurements between the TMC6300 and the gimabal motor.
* The MCP6021 is used on the low-side current measurement of the TMC63000's half-bridges.

<center>

| **Current Sensor** | INA240 *(`U`)* | INA240 *(`V`)* | INA240 *(`W`)* | MCP6021 |
| :--- | :---: | :---: | :---: | :---: |
| **Analog Input** | `GPIO 35` | `GPIO 36` | `GPIO 39` | `GPIO 32` |

</center>

### :fontawesome-solid-microchip:&nbsp;Inline - INA240
The [INA240](./assets/component_documentation/INA240.pdf) from [Texas Instruments](https://www.ti.com/), is a voltage-output, current-sense amplifier. For more information, please refer to the [INA240 datasheet](./assets/component_documentation/INA240.pdf).

<div class="grid cards col-4" markdown align="center">

-   <figure markdown>
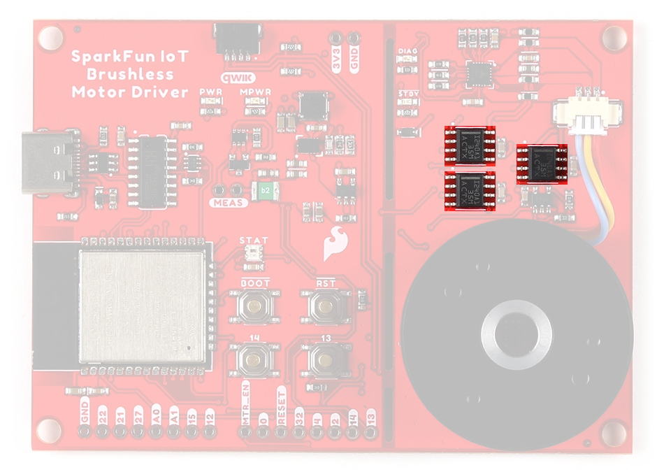
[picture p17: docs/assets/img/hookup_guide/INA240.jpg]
	
	<figcaption markdown>The INA240 current-sense amplifier on the IoT Motor Driver.</figcaption>
	</figure>

-   <table>
		<tr>
			<td>Configured Gain</td>
			<td>20 &PlusMn;0.2%</td>
		</tr>
		<tr>
			<td>Bandwidth</td>
			<td>100kHz</td>
		</tr>
		<tr>
			<td>Voltage Range</td>
			<td>Range: 2.7 - 5.5V</td>
		</tr>
		<tr>
			<td>Quiescent Current</td>
			<td>1.8 - 2.6mA</td>
		</tr>
		<tr>
			<td>Operating Temperature</td>
			<td>–40 - 125&deg;C</td>
		</tr>
	</table>

</div>

### :fontawesome-solid-microchip:&nbsp;Low-side Op Amp - MCP6021
The [MCP6021](./assets/component_documentation/MCP6021.pdf) from [Microchip Technology, Inc.](https://www.microchip.com/), is a rail-to-rail input and output operational amplifier. The chip . For more information, please refer to the [MCP6021 datasheet](./assets/component_documentation/MCP6021.pdf).

<div class="grid cards col-4" markdown align="center">

-   <figure markdown>
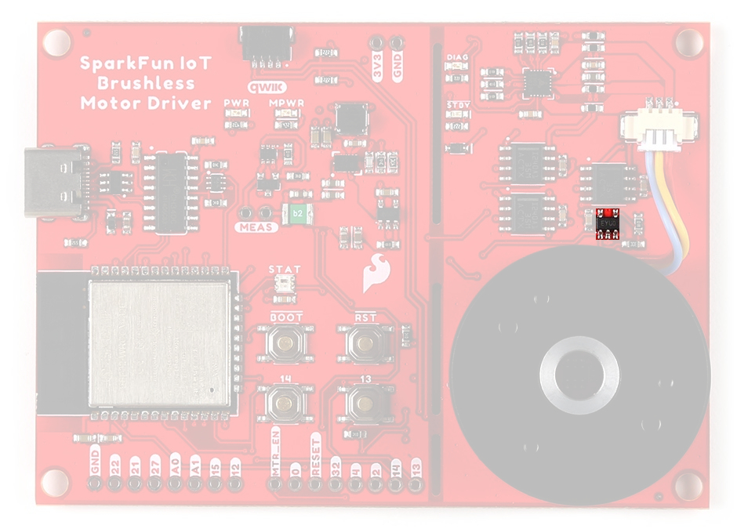
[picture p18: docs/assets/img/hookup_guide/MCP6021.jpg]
	
	<figcaption markdown>The MCP6021 Op Amp on the IoT Motor Driver.</figcaption>
	</figure>

-   <table>
		<tr>
			<td>Configured Gain</td>
			<td>21</td>
		</tr>
		<tr>
			<td>Bandwidth</td>
			<td>10MHz</td>
		</tr>
		<tr>
			<td>Voltage Range</td>
			<td>Range: 2.5 - 5.5V</td>
		</tr>
		<tr>
			<td>Quiescent Current</td>
			<td>0.5 - 1.35mA</td>
		</tr>
		<tr>
			<td>Operating Temperature</td>
			<td>–40 - 125&deg;C</td>
		</tr>
	</table>

</div>

## Status LEDs
There are five status LEDs on the TMC6300 motor driver:

* `PWR` - Power *(Red)*
	* Turns on once power is supplied through the USB-C connector
* `MPWR` - Power *(Red)*
	* Turns on once power is supplied through the USB-C connector
* `DIAG` - Diagnostics *(Green)*
	* Turns on to indicate a fault *(see [diagnostic pin](#diagnostic-pin) section)*
* `STBY` - Standby *(Blue)*
	* Turns on when the motor driver is enabled
	* Turns off, when the IC has been reset and the motor driver is in standby mode
* `STAT` - User *(RGB)*
	* Controlled through `GPIO 02`

<figure markdown>
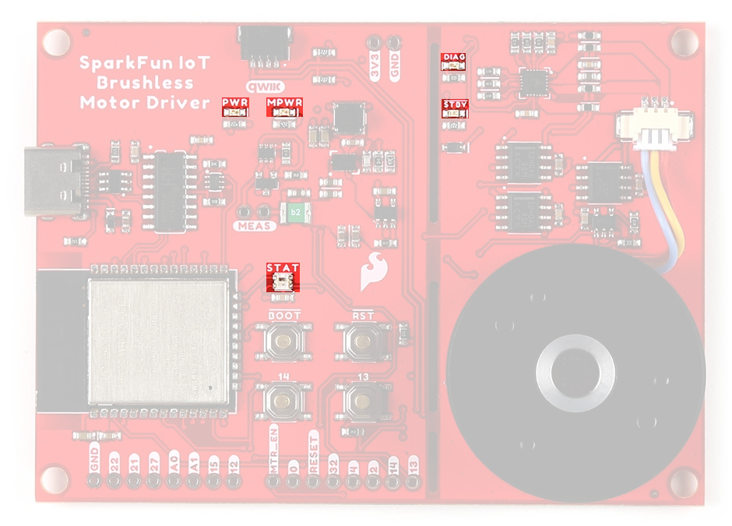
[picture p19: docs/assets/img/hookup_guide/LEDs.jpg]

<figcaption markdown>
The status indicator LEDs on the TMC6300 motor driver.
</figcaption>
</figure>

### WS2812 RGB LED
The WS2812 RGB LED is controlled with a 24-bit (GRB) data signal. This indicator is connected to `GPIO 02` and the digital output pin from the LED is available through a test point. For more information, please refer to the [WS2812C datasheet](./assets/component_documentation/WS2812.pdf).

<figure markdown>
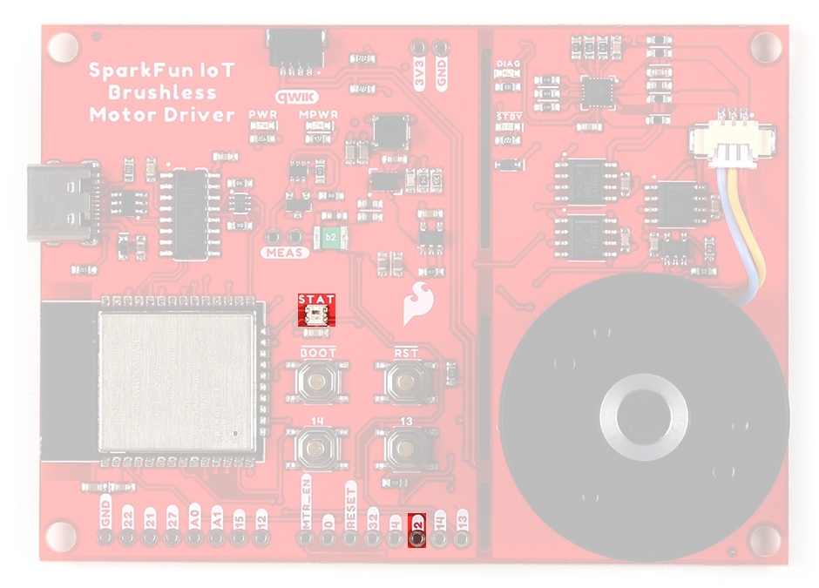
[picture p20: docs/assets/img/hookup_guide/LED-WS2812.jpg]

<figcaption markdown>The status indicator LED (`STAT`)on the IoT Motor Driver.</figcaption>
</figure>

!!! info
	The latest ESP32 Arduino core, now provides a basic RGB LED driver for a WS2812 *(or NeoPixel)* LED populated the board. For an example of how to utilize the RGB LED driver check out the [BlinkRGB example code](https://github.com/espressif/arduino-esp32/blob/master/libraries/ESP32/examples/GPIO/BlinkRGB/BlinkRGB.ino), which can be accessed from the File drop down menu *(i.e **File** > **Examples** > **ESP32** > **GPIO** > **BlinkRGB**)*.

## Buttons
There are four buttons on IoT Motor Driver: ++"RST"++, ++"BOOT"++, ++"13"++, and ++"14"++ buttons.

<figure markdown>
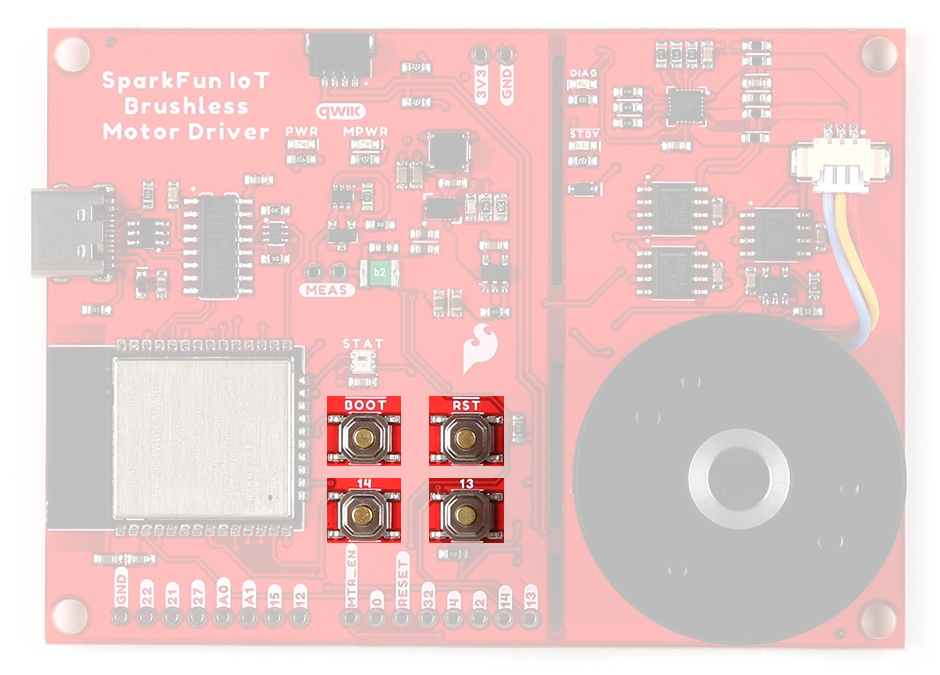
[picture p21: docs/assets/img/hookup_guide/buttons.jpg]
Buttons

<figcaption markdown>Buttons on the IoT Motor Driver.</figcaption>
</figure>

??? tip "Factory Programming"
	The IoT Motor Driver board will come pre-programmed out of the bag. By default, the ++"13"++/++"14"++ buttons can be used to operate the motor:
  
	* ++"13"++ - Start/Stop the motor's rotation
	* ++"14"++ - Switch the direction that the motor is spinning

#### Reset Button
The ++"RST"++ *(reset)* button allows users to reset the program running on the ESP32-WROOM module without unplugging the board.

<figure markdown>
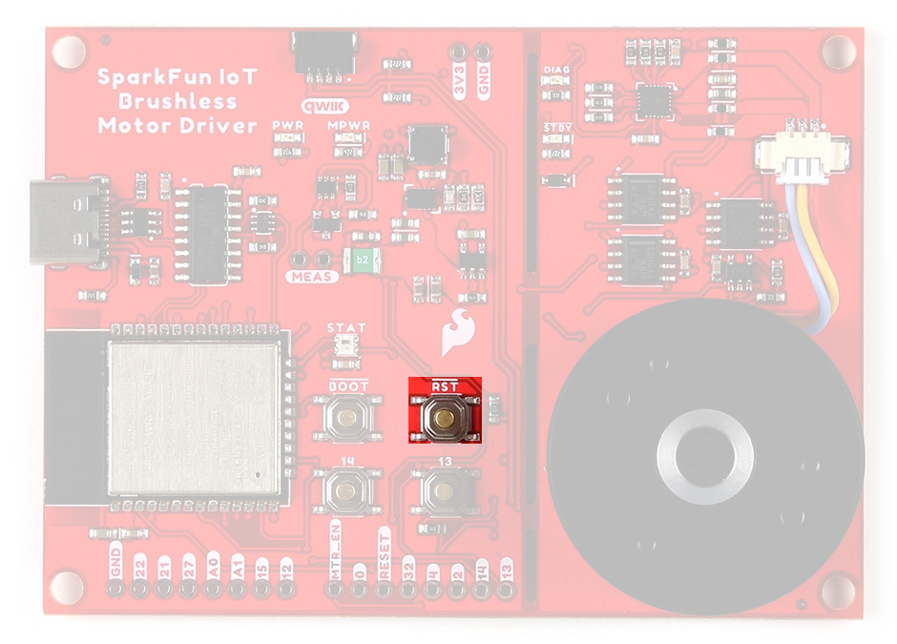
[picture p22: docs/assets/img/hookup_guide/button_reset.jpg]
Reset Button

<figcaption markdown>++"RST"++ button on the IoT Motor Driver.</figcaption>
</figure>

#### Boot Control
The ++"BOOT"++ button can be used to force the board into the serial bootloader. Holding down the ++"BOOT"++ button, while connecting the board to a computer through its USB-C connector or resetting the board will cause it to enter the <a href="https://docs.espressif.com/projects/esptool/en/latest/esp32/advanced-topics/boot-mode-selection.html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">Firmware Download mode</a>. The board will remain in this mode until it power cycles (happens automatically after uploading new firmware) or the ++"RST"++ button is pressed.

1. Hold the ++"BOOT"++ button down.
2. Reset the MCU.
	* While unpowered, connect the board to a computer with through the USB-C connection.
	* While powered, press the ++"RST"++ button.
3. Release the ++"BOOT"++ button.
4. After programming is completed, reboot the MCU.
	* Press the ++"RST"++ button.
	* Power cycle the board.

<figure markdown>
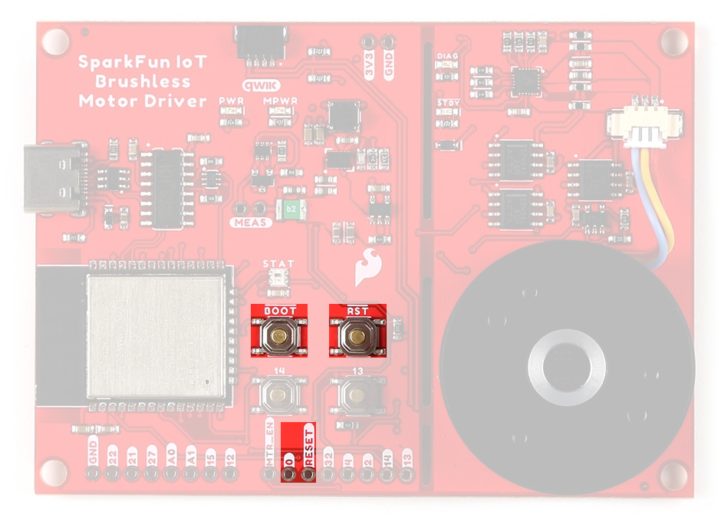
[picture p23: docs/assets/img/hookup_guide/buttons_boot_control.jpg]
Boot Button

<figcaption markdown>++"BOOT"++ button on the IoT Motor Driver.</figcaption>
</figure>

!!! info
	**&#9889;** The ++"BOOT"++ button is also connected to `GPIO 0`.

### User Buttons
The ++"13"++ and ++"14"++ buttons are available for users to configure for their own purposes.

<figure markdown>
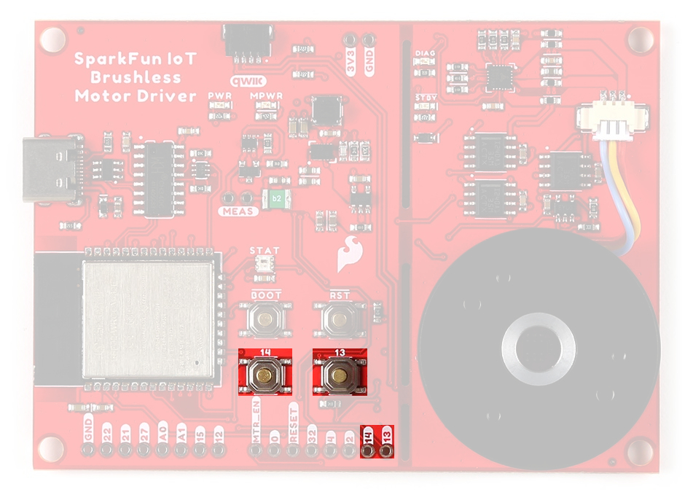
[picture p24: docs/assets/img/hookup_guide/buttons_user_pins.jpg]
User Buttons

<figcaption markdown>The user buttons (++"13"++ and ++"14"++) on the IoT Motor Driver.</figcaption>
</figure>

!!! tip "Factory Programming"
	The IoT Motor Driver board will come pre-programmed out of the bag. By default, these buttons can be used to operate the motor:
  
	* ++"13"++ - Start/Stop the motor's rotation
	* ++"14"++ - Switch the direction that the motor is spinning

!!! tip
	When utilizing the buttons, users should enable the internal pull-up resistors for the GPIO pins.

## Jumpers

??? note "Never modified a jumper before?"
	Check out our <a href="https://learn.sparkfun.com/tutorials/664">Jumper Pads and PCB Traces tutorial</a> for a quick introduction!

	<div class="grid cards col-4" markdown align="center">

	-   <a href="https://learn.sparkfun.com/tutorials/664">
		<figure markdown>
		Tutorial thumbnail
		</figure>

		---
		
		**How to Work with Jumper Pads and PCB Traces**</a>

	</div>

There are nine jumpers on the back of the board that can be used to easily modify a hardware connections on the board.

* **SHLD** - This jumper can be used to disconnect the shield of the USB-C connector from `GND`.
* **MEAS** - This jumper can be used to measure the current consumption of the board.
* **BYP** - This jumper can be used to bypass the thermal fuse.
* LED Jumpers
	* **PWR** - This jumper can be used to remove power from the red, power LED on the AP2112 LDO regulator.
	* **MPWR** - This jumper can be used to remove power from the red, power LED on the AP63357 LDO regulator.
	* **STBY** - This jumper can be used to remove power from the blue, standby LED.
	* **DIAG** - This jumper can be used to remove power from the green, diagnostic LED.
* **INT** - This jumper can be used to remove the pull-up resistor from the `INT` pin of the hall-effect sensor.
* **I2C** - This jumper can be used to remove the pull-up resistors on the I<sup>2</sup>C bus.

<figure markdown>
Jumpers
<figcaption markdown>
The jumpers on the back of the IoT Motor Driver.
</figcaption>
</figure>

## Primary I<sup>2</sup>C Bus
The Qwiic connector and hall-effect sensor are attached to the primary I<sup>2</sup>C bus. The primary I<sup>2</sup>C bus for this board utilizes the pin connections, detailed in the table below:

<figure markdown>
I2C connections
<figcaption markdown>I<sup>2</sup>C bus connections on the IoT Motor Driver.</figcaption>
</figure>

<p><center>
	<table>
		<tr>
			<th style="text-align:center">
				Connection
			</th>
			<td align="center"><code>VDD</code></td>
			<td align="center"><code>GND</code></td>
			<td align="center"><code>SCL</code></td>
			<td align="center"><code>SDA</code></td>
		</tr>
		<tr>
			<th style="text-align:center; vertical-align:middle">
				Hall-Effect Sensor<br>
				<i>(TMAG5273)</i>
			</th>
			<td style="text-align:center; vertical-align:middle"><code>3V3</code></td>
			<td style="text-align:center; vertical-align:middle"><b>GND</b></td>
			<td style="text-align:center; vertical-align:middle"><code>GPIO 22</code></td>
			<td style="text-align:center; vertical-align:middle"><code>GPIO 21</code></td>
		</tr>
		<tr>
			<th style="text-align:center; vertical-align:middle">
				Qwiic Connector
			</th>
			<td style="text-align:center; vertical-align:middle"><code>3V3</code></td>
			<td style="text-align:center; vertical-align:middle"><b>GND</b></td>
			<td style="text-align:center; vertical-align:middle"><code>GPIO 22</code></td>
			<td style="text-align:center; vertical-align:middle"><code>GPIO 21</code></td>
		</tr>
	</table>
</center></p>

### Qwiic Connector
A Qwiic connector is provided for users to seamlessly integrate with <a href="https://www.sparkfun.com/qwiic">SparkFun's Qwiic Ecosystem</a>. Otherwise, users can connect their I<sup>2</sup>C devices through the PTH pins broken out on the board.

<figure markdown>
Qwiic connector and I2C pins
<figcaption markdown>Qwiic connector and I<sup>2</sup>C pins on the IoT Motor Driver.</figcaption>
</figure>

??? tip "What is Qwiic?"

	<!-- Qwiic Banner -->
	<center>
	Qwiic Logo - light theme (https://www.sparkfun.com/qwiic)
	Qwiic Logo - dark theme (https://www.sparkfun.com/qwiic)
	</center>
	
	---
	
	The [Qwiic connect system](https://www.sparkfun.com/qwiic) is a solderless, polarized connection system that allows users to seamlessly daisy chain I<sup>2</sup>C boards together. Play the video below to learn more about the Qwiic connect system or click on the banner above to learn more about [Qwiic products](https://www.sparkfun.com/qwiic).

	<center>
	<div class="video">
	<iframe src="https://www.youtube.com/embed/x0RDEHqFIF8" title="SparkFun's Qwiic Connect System" frameborder="0" allow="accelerometer; encrypted-media; gyroscope; picture-in-picture" allowfullscreen></iframe>
	</div>
	</center>

	!!! info "Features of the Qwiic System"

		=== "No Soldering"

			no soldering - light theme
			no soldering - dark theme

			Qwiic cables (4-pin JST) plug easily from development boards to sensors, shields, accessory boards and more, making easy work of setting up a new prototype.

		=== "Polarized Connector"
	
			polarized connector - light theme
			polarized connector - dark theme

			There's no need to worry about accidentally swapping the SDA and SCL wires on your breadboard. The Qwiic connector is polarized so you know you’ll have it wired correctly 	every time, right from the start.

			The PCB connector is part number SM04B-SRSS ([Datasheet](https://cdn.sparkfun.com/assets/parts/1/2/2/8/9/Qwiic_Connector_Datasheet.pdf)) or equivalent. The mating connector used on cables is part number SHR04V-S-B or an equivalent *(1mm pitch, 4-pin JST connector)*.
	
		=== "Daisy Chain-able"

			daisy chainable - light theme
			daisy chainable - dark theme
	
			It’s time to leverage the power of the I<sup>2</sup>C bus! Most Qwiic boards will have two or more connectors on them, allowing multiple devices to be connected.

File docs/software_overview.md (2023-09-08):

---
icon: simple/arduino
---

## CH340 Driver
Users will need to install the appropriate driver for their computer to recognize the serial-to-UART chip on their board/adapter. Most of the latest operating systems will recognize the CH340C chip on the board and automatically install the required driver.

*To manually install the CH340 driver on their computer, users can download it from the [WCH website](http://www.wch-ic.com/products/CH340.html?). For more information, check out our [How to Install CH340 Drivers Tutorial](https://www.sparkfun.com/ch340).*

<figure markdown>
How to Install CH340 Drivers (https://learn.sparkfun.com/tutorials/908)
<figcaption markdown>[**How to Install CH340 Drivers**](https://learn.sparkfun.com/tutorials/908)</figcaption>
</figure>

## Arduino IDE
!!! tip
	For first-time users, who have never programmed before and are looking to use the Arduino IDE, we recommend beginning with the <a href="https://www.sparkfun.com/products/15631">SparkFun Inventor's Kit (SIK)</a>, which is designed to help users get started programming with the Arduino IDE.

Most users may already be familiar with the Arduino IDE and its use. However, for those of you who have never heard the name *Arduino* before, feel free to check out the [Arduino website](https://www.arduino.cc/en/Guide/HomePage). To get started with using the Arduino IDE, check out our tutorials below:

<div class="grid cards" markdown align="center">

-   <a href="https://learn.sparkfun.com/tutorials/50"><figure markdown>
	What is an Arduino?
	</figure>

	---

	**What is an Arduino?**</a>

-   <a href="https://learn.sparkfun.com/tutorials/61"><figure markdown>
	Installing the Arduino IDE
	</figure>

	---
	
	**Installing the Arduino IDE**</a>

-   <a href="https://learn.sparkfun.com/tutorials/15"><figure markdown>
	Installing an Arduino Library
	</figure>

	---
	
	**Installing an Arduino Library**</a>

-   <a href="https://learn.sparkfun.com/tutorials/1265"><figure markdown>
	Installing Board Definitions in the Arduino IDE
	</figure>

	---
	
	**Installing Board Definitions in the Arduino IDE**</a>
</div>

### Install Board Definition
Install the latest <b>ESP32</b> board definitions in the Arduino IDE.

<center>
Installing Board Definitions in the Arduino IDE (https://learn.sparkfun.com/tutorials/1265)<br>
[**Installing Board Definitions in the Arduino IDE**](https://learn.sparkfun.com/tutorials/1265)
</center>

!!! info
	For more instructions, users can follow this tutorial on [Installing Additional Cores](https://docs.arduino.cc/learn/starting-guide/cores) provided by Arduino. Users will also need the `.json` file for the Espressif Arduino core:

		https://raw.githubusercontent.com/espressif/arduino-esp32/gh-pages/package_esp32_index.json

When selecting a board to program in the Arduino IDE, users should select the **SparkFun ESP32 Thing Plus C** from the `Tools` drop-down menu _(_i.e. **Tools** > **Board** > **ESP32 Arduino** > **SparkFun ESP32 Thing Plus C**)._ Alternatively, users can also select the **ESP32 Dev Module**; however, they may lose some pin assignments.

<figure markdown>
Click to enlarge
<figcaption markdown>Select the **SparkFun ESP32 Thing Plus C** from the `Tools` drop-down menu in the Arduino IDE.</figcaption>
</figure>

??? info "Arduino IDE 2.x.x - *Alternative Method*"
	In the newest version of the Arduino IDE 2.`x`.`x`, users can also select their board (*green*) and port (*blue*) from the `Select Board & Port` dropdown menu (*yellow*).

	<figure markdown>
	Click to enlarge
	<figcaption markdown>Selecting the **SparkFun ESP32 Thing Plus C** and **COM5** port from the **Select Board & Port** drop-down menu in the Arduino IDE (v2.0.3).</figcaption>
	</figure>

<!-- Comment Out

??? tip "Arduino IDE *(v1.x.x)*"
	In the Arduino IDE v1.x.x, users will select the **SparkFun ESP32 Thing Plus C** from the `Tools` drop-down menu _(_i.e. **Tools** > **Board** > **ESP32 Arduino** > **SparkFun ESP32 Thing Plus C**)._

	<figure markdown>
	[![](./assets/img/hookup_guide/board_selection-legacy.png "Click to enlarge"){ width="400" }](./assets/img/hookup_guide/board_selection-legacy.png)
	<figcaption markdown>Selecting the **SparkFun ESP32 Thing Plus C** from the **Tools** drop-down menu in the Arduino IDE (v1.8.19).</figcaption>
	</figure>
-->

## SparkFun TMAG5273 Arduino Library
The [SparkFun TMAG5273 Arduino Library](https://github.com/sparkfun/SparkFun_TMAG5273_Arduino_Library) can be installed from the library manager in the Arduino IDE.

<figure markdown>
Click to enlarge
<figcaption markdown>SparkFun TMAG5273 Arduino library in the library manager of the Arduino IDE.</figcaption>
</figure>

??? tip "Arduino IDE *(v1.x.x)*"
	In the Arduino IDE v1.x.x, the library manager will have the following appearance for the SimpleFOC library:

	<figure markdown>
	Click to enlarge
	<figcaption markdown>SparkFun TMAG5273 Arduino library in the library managerof the Arduino IDE (v1.x.x).</figcaption>
	</figure>

This library will be primarily used to interact with the TMAG5273 hall-effect sensor and return the rotation angle of the motor.

## SimpleFOC Arduino Library
The [Simple Field Oriented Control Library](https://github.com/simplefoc/Arduino-FOC) can be installed from the library manager in the Arduino IDE.

<figure markdown>
Click to enlarge
<figcaption markdown>SimpleFOC library in the library manager of the Arduino IDE.</figcaption>
</figure>

??? tip "Arduino IDE *(v1.x.x)*"
	In the Arduino IDE v1.x.x, the library manager will have the following appearance for the SimpleFOC library:

	<figure markdown>
	Click to enlarge
	<figcaption markdown>SimpleFOC library in the library manager of the Arduino IDE (v1.x.x).</figcaption>
	</figure>

This library utilizes a motor control scheme called field oriented control (FOC), which can utilize a feedback control loop to drive a motor with a higher power efficiency and precision characteristics, like evenly distributed torque control.

!!! info
	For more details about the library, check out the [online documentation](https://docs.simplefoc.com/).

!!! note "Supported Hardware"
	For a detailed and up-to-date list of the hardware supported by this library, check out the [library's documentation](https://docs.simplefoc.com/supported_hardware). The following are excerpts taken from the library's documentation page:

	=== "Microcontrollers"

		--8<-- "https://raw.githubusercontent.com/simplefoc/simplefoc.github.io/master/docs/simplefoc_library/hardware/mcus/index.md:14:15"

		--8<-- "https://raw.githubusercontent.com/simplefoc/simplefoc.github.io/master/docs/simplefoc_library/hardware/mcus/index.md:35:49"

		!!! info
			For more details, please refer to the [SimpleFOC Arduino library documentation](https://docs.simplefoc.com/microcontrollers).
	
	=== "Motor Drivers"

		--8<-- "https://raw.githubusercontent.com/simplefoc/simplefoc.github.io/master/docs/simplefoc_library/hardware/drivers/index.md:19:23"

		??? warning "Current Limitations"
			--8<-- "https://raw.githubusercontent.com/simplefoc/simplefoc.github.io/master/docs/simplefoc_library/hardware/drivers/index.md:30"

		!!! tip
			While the TMC6300 isn't directly listed as part of the supported hardware for the SimpleFOC Arduino library, we have verified that is compatible with the library.

		!!! info
			For more details, please refer to the [SimpleFOC Arduino library documentation](https://docs.simplefoc.com/bldc_drivers).

	=== "Motors"

		Arduino SimpleFOClibrary supports two types of BLDC motors:

		- BLDC motors
			- 3 phase (3 wire):

				??? info "Gimbal Motors"
					--8<-- "https://raw.githubusercontent.com/simplefoc/simplefoc.github.io/master/docs/simplefoc_library/hardware/motors/BLDC_motors.md:20:22"

					--8<-- "https://raw.githubusercontent.com/simplefoc/simplefoc.github.io/master/docs/simplefoc_library/hardware/motors/BLDC_motors.md:23:28"

				??? info "High-performance Motors"		
					--8<-- "https://raw.githubusercontent.com/simplefoc/simplefoc.github.io/master/docs/simplefoc_library/hardware/motors/BLDC_motors.md:43:43"
		- Stepper motors
			- 2 phase (4 wire)
	
		??? warning "Current Limitations"
			--8<-- "https://raw.githubusercontent.com/simplefoc/simplefoc.github.io/master/docs/simplefoc_library/hardware/motors/index.md:28"

		!!! info
			For more details, please refer to the [SimpleFOC Arduino library documentation](https://docs.simplefoc.com/bldc_motors).

### 6PWM Motor Driver

Users will need to utilize the [`BLDCDriver6PWM` class](https://docs.simplefoc.com/bldcdriver6pwm) to provide the six PWM signals required for the TMC6300 motor driver.

`BLDCDriver6PWM`

:   This class provides an abstraction layer for most of the common BLDC drivers, which require six PWM signals. This method offers more control than a three PWM motor drivers, since each of the 6 half-bridges MOSFETs can be controlled independently.

	--8<-- "https://raw.githubusercontent.com/simplefoc/simplefoc.github.io/master/docs/simplefoc_library/code/drivers/bldc_driver/bldc_driver_6pwm.md:28:36"

	!!! note "Microcontroller Considerations"
		=== "Arduino Uno"
			--8<-- "https://raw.githubusercontent.com/simplefoc/simplefoc.github.io/master/docs/simplefoc_library/code/drivers/bldc_driver/bldc_driver_6pwm.md:42:50"

		=== "STM32"
			--8<-- "https://raw.githubusercontent.com/simplefoc/simplefoc.github.io/master/docs/simplefoc_library/code/drivers/bldc_driver/bldc_driver_6pwm.md:54:54"

			--8<-- "https://raw.githubusercontent.com/simplefoc/simplefoc.github.io/master/docs/simplefoc_library/code/drivers/bldc_driver/bldc_driver_6pwm.md:55:56"

			<div class="grid cards" markdown>

			-   **Hardware PWM**

				---

				--8<-- "https://raw.githubusercontent.com/simplefoc/simplefoc.github.io/master/docs/simplefoc_library/code/drivers/bldc_driver/bldc_driver_6pwm.md:59:69"

			-   **Software PWM**

				---

				--8<-- "https://raw.githubusercontent.com/simplefoc/simplefoc.github.io/master/docs/simplefoc_library/code/drivers/bldc_driver/bldc_driver_6pwm.md:72:93"

			</div>

		=== "ESP32"
			--8<-- "https://raw.githubusercontent.com/simplefoc/simplefoc.github.io/master/docs/simplefoc_library/code/drivers/bldc_driver/bldc_driver_6pwm.md:96:96"

	!!! info
		For more details about the `BLDCDriver6PWM` class, check out the [online documentation](https://docs.simplefoc.com/bldcdriver6pwm).

<!-- 
The PWM carrier frequency used to control the motor driver can greatly affect its efficiency.

* Low frequency - poor current shape, which increased heating and harmonics loss in the motor
* High frequency - increased transistor switching loss -->

### BLDC Motor

All BLDC motors are handled with the [`BLDCMotor` class](https://docs.simplefoc.com/bldcmotor).

`BLDCMotor`

:   This class implements the BLDC FOC algorithm, motion control loops, and monitoring.

	--8<-- "https://raw.githubusercontent.com/simplefoc/simplefoc.github.io/master/docs/simplefoc_library/code/motors/bldc_motors.md:23:30"

	!!! note "Motor Considerations"
		While, the datasheet for our [gimbal motor](https://www.sparkfun.com/products/20441), indicates that there are **8 pole pairs**, we have found that the motor operates more smoothly if the `BLDCMotor` class is instantiated with **7 pole pairs** instead.

		```cp
		BLDCMotor motor = BLDCMotor(7);
		```

	!!! info
		For more details about the `BLDCMotor` class, check out the [online documentation](https://docs.simplefoc.com/bldcmotor).

### Position Sensor
In order to incorporate the TMAG5273 hall-effect sensor into the FOC algorithm, users will need to utilize the [`GenericSensor` class](https://docs.simplefoc.com/generic_sensor).

`GenericSensor`

:   This class allows users to link a custom position sensor *(not already implemented in the SimpleFOC library)* by incorporating a few functions into their sketch.

	1. Implement two functions; one to initialize the TMAG5273 and another to read and return the sensor's current position.

		--8<-- "https://github.com/simplefoc/simplefoc.github.io/raw/master/docs/simplefoc_library/code/sensors/generic.md:29:33"

		--8<-- "https://github.com/simplefoc/simplefoc.github.io/raw/master/docs/simplefoc_library/code/sensors/generic.md:20:26"

	2. Instantiate the `GenericSensor` class and initialize the class by providing it pointers to the two functions.

		--8<-- "https://github.com/simplefoc/simplefoc.github.io/raw/master/docs/simplefoc_library/code/sensors/generic.md:37:42"

	3. There are two ways to use sensors implemented within the SimpleFOC library:
		* As standalone position sensor
			* In this configuration users would simply read the sensor's position, independently from incorporating the readings into the FOC algorithm.
		* Incorporate it as the motor position sensor for FOC algorithm

			1. Initialize the sensor in the `setup()` loop:

				```cpp
				--8<-- "https://github.com/simplefoc/simplefoc.github.io/raw/master/docs/simplefoc_library/code/sensors/generic.md:88:97"
				```

			2. Link the sensor in the `setup()` loop:

				```cpp
				--8<-- "https://github.com/simplefoc/simplefoc.github.io/raw/master/docs/simplefoc_library/code/sensors/generic.md:138:147"
				```

!!! info
	For more instructions on incorporating the `GenericSensor` class, please refer to the [SimpleFOC documentation](https://docs.simplefoc.com/generic_sensor).

### In-line Current Sensing
In order to incorporate the current sensing into the FOC algorithm, users will need to utilize the [`InlineCurrentSense` class](https://docs.simplefoc.com/inline_current_sense).

`InlineCurrentSense`

:   This class allows users to link a custom position sensor *(not already implemented in the SimpleFOC library)* by incorporating a few functions into their sketch.

	1. Instantiate the `InlineCurrentSense` class and initialize the class by providing the hardware configuration.

		--8<-- "https://github.com/simplefoc/simplefoc.github.io/raw/master/docs/simplefoc_library/code/current_sense/inline.md:38:46"

	2. Incorporate the current sensor into the FOC algorithm:

		1. Initialize the sensor in the `setup()` loop:

			--8<-- "https://github.com/simplefoc/simplefoc.github.io/raw/master/docs/simplefoc_library/code/current_sense/inline.md:100:103"

		2. Link the sensor to the motor driver in the `setup()` loop:

			--8<-- "https://github.com/simplefoc/simplefoc.github.io/raw/master/docs/simplefoc_library/code/current_sense/inline.md:126:129"
		
		2. Link the sensor to the motor in the `setup()` loop:

			--8<-- "https://github.com/simplefoc/simplefoc.github.io/raw/master/docs/simplefoc_library/code/current_sense/inline.md:138:141"

		--8<-- "https://github.com/simplefoc/simplefoc.github.io/raw/master/docs/simplefoc_library/code/current_sense/inline.md:145:168"

!!! info
	For instructions on incorporating the `InlineCurrentSense` class, please refer to the [SimpleFOC documentation](https://docs.simplefoc.com/inline_current_sense).

<!-- ### Motion Control

Unless a feedback loop is incorporated when driving the motor *(i.e. with [position sensors](https://docs.simplefoc.com/sensors) or [current sensing](https://docs.simplefoc.com/current_sense))*, users should implement the SimpleFOC library using the [open-loop control](https://docs.simplefoc.com/open_loop_motion_control).

Open-Loop Motion Control Types:

* [Velocity](https://docs.simplefoc.com/velocity_openloop)
* [Position](https://docs.simplefoc.com/angle_openloop) -->

<!-- #### Sensorless FOC
Current measurement

#### Closed-Loop
With position sensors

Control Types (available in library):
* Torque
* Velocity
* Angle

#### Low-side current sensing

While the SimpleFOC Arduino library offers the option to incorporate low-side current sensors into the feedback loop, 

--8<-- "https://raw.githubusercontent.com/simplefoc/simplefoc.github.io/master/docs/simplefoc_library/code/drivers/bldc_driver/bldc_driver_6pwm.md:101:110"

utilizing the [open loop example](https://github.com/simplefoc/Arduino-FOC/blob/master/examples/motion_control/open_loop_motor_control/open_loop_velocity_example/open_loop_velocity_example.ino) combined with the [6 channel PWM method](https://docs.simplefoc.com/bldcdriver6pwm) and *every* PWM pin on the Arduino Uno gets this board working. Note the [pairs of PWM pins](https://docs.simplefoc.com/bldcdriver6pwm) that must be used. -->

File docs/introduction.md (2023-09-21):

---
icon: material/book-open-page-variant
---

# Introduction
<div class="grid cards desc" markdown>

-   <a href="https://www.sparkfun.com/products/22132">
	**IoT Brushless Motor Driver**<br>
	**SKU:** ROB-22132
	
	---
	
	<figure markdown>
	Product Thumbnail
	</figure></a>

	<center>
	<article class="video_desc">
	<iframe src="https://www.youtube.com/embed/4GGIxnUDrU0" title="Product Showcase: SparkFun IoT Brushless Motor Driver (ESP32 WROOM, TMC6300)" frameborder="0" allow="accelerometer; autoplay; clipboard-write; encrypted-media; gyroscope; picture-in-picture" allowfullscreen></iframe>
	</article>
	QR code to play video
	</center>

-	The SparkFun IoT Brushless Motor Driver is an all-in-one development platform. It includes all the components to create a simple IoT device or learn about [control systems](https://en.wikipedia.org/wiki/Control_system). On the boaard, users will find an ESP32 microcontroller, a TMC6300 motor driver, a [gimbal motor](https://www.sparkfun.com/products/20441), a TMAG5273 hall-effect sensor, three INA240A1 inline current sensors, an MCP6021T low-side current sensor, two user buttons, a Qwiic connector, a 3-pin JST connector (for the gimbal motor), and a WS2812 RGB LED.

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

	<center>
	[QR code to product page&nbsp;&nbsp;&nbsp;Purchase from SparkFun :fontawesome-solid-cart-plus:{ .heart }](https://www.sparkfun.com/products/22132){ .md-button .md-button--primary }
	</center>

</div>

## :fontawesome-solid-list-check:&nbsp;Required Materials
To get started, users will need a few items. Now some users may already have a few of these items, feel free to modify your cart accordingly.

* Computer with an operating system (OS) that is compatible with all the software installation requirements.
* [USB 3.1 Cable A to C - 3 Foot](https://www.sparkfun.com/products/14743) - Used to interface with the IoT Brushless Motor Driver (1)
{ .annotate }

	1.	If your computer doesn't have a USB-A slot, then choose an appropriate cable or adapter.

* [SparkFun IoT Brushless Motor Driver (ESP32 WROOM, TMC6300)](https://www.sparkfun.com/products/22132) (1)
{ .annotate }

	1. The included gimbal motor requires a 6 to 8V power supply. However, for zero-load, low-speed testing, we have found the power from the USB connection to be sufficient.

<div class="grid cards col-4" markdown>

-   <a href="https://www.sparkfun.com/products/14743">
	<figure markdown>
	USB 3.1 Cable A to C - 3 Foot
	</figure>

	---

	**USB 3.1 Cable A to C - 3 Foot**<br>
	CAB-14743</a>

-   <a href="https://www.sparkfun.com/products/22132">
	<figure markdown>
	Product Thumbnail
	</figure>

	---

	**IoT Brushless Motor Driver (ESP32 WROOM, TMC6300)**<br>
	ROB-22132</a>

</div>

??? note "Jumper Modification"
	To modify the [jumper](hardware_overview/#jumper), users will need [soldering equipment](https://www.sparkfun.com/categories/49) and/or a [hobby knife](https://www.sparkfun.com/categories/379).

	!!! tip "New to jumper pads?"
		Check out our [Jumper Pads and PCB Traces Tutorial](https://learn.sparkfun.com/tutorials/664) for a quick introduction!

		<div class="grid cards col-4" markdown  align="center">

		-   <a href="https://learn.sparkfun.com/tutorials/664">
			<figure markdown>
			Tutorial thumbnail
			</figure>

			---
			
			**How to Work with Jumper Pads and PCB Traces**</a>

		</div>

	<div class="grid cards col-4" markdown>

	-   <a href="https://www.sparkfun.com/products/9325">
		<figure markdown>
		Product Thumbnail
		</figure>		

		---

		**Solder Lead Free - 100-gram Spool**<br>
		TOL-09325</a>

	-   <a href="https://www.sparkfun.com/products/14228">
		<figure markdown>
		Product Thumbnail
		</figure>

		---
		
		**Weller WLC100 Soldering Station**<br>
		TOL-14228</a>

	-   <a href="https://www.sparkfun.com/products/14579">
		<figure markdown>
		Product Thumbnail
		</figure>

		---

		**Chip Quik No-Clean Flux Pen - 10mL**<br>
		TOL-14579</a>

	-   <a href="https://www.sparkfun.com/products/9200">
		<figure markdown>
		Product Thumbnail
		</figure>

		---

		**Hobby Knife**<br>
		TOL-09200</a>
	</div>

## :material-bookshelf:&nbsp;Suggested Reading

As a more sophisticated product, we will skip over the more fundamental tutorials (i.e. [**Ohm's Law**](https://learn.sparkfun.com/tutorials/voltage-current-resistance-and-ohms-law) and [**What is Electricity?**](https://learn.sparkfun.com/tutorials/what-is-electricity)). However, below are a few tutorials that may help users familiarize themselves with various aspects of the board.

<div class="grid cards col-4" markdown align="center">

-   <a href="https://learn.sparkfun.com/tutorials/908">
	<figure markdown>
	Tutorial Thumbnail
	</figure>

	---
	
	**How to Install CH340 Drivers**</a>

-   <a href="https://learn.sparkfun.com/tutorials/2353">
	<figure markdown>
	Tutorial Thumbnail
	</figure>

	---
	
	**ESP32 Thing Plus (USB-C)**</a>

-   <a href="http://docs.sparkfun.com/SparkFun_Three_Phase_Motor_Driver-TMC6300/">
	<figure markdown>
	Tutorial Thumbnail
	</figure>

	---
	
	**TMC6300 BLDC Motor Driver**</a>

-   <a href="https://learn.sparkfun.com/tutorials/61">
	<figure markdown>
	Tutorial Thumbnail
	</figure>

	---
	
	**Installing the Arduino IDE**</a>

-   <a href="https://learn.sparkfun.com/tutorials/1265">
	<figure markdown>
	Tutorial Thumbnail
	</figure>

	---
	
	**Installing Board Definitions in the Arduino IDE**</a>

-   <a href="https://learn.sparkfun.com/tutorials/15">
	<figure markdown>
	Tutorial Thumbnail
	</figure>

	---
	
	**Installing an Arduino Library**</a>

-   <a href="https://learn.sparkfun.com/tutorials/62">
	<figure markdown>
	Tutorial Thumbnail
	</figure>

	---
	
	**Logic Levels**</a>

-   <a href="https://learn.sparkfun.com/tutorials/51">
	<figure markdown>
	Tutorial Thumbnail
	</figure>

	---
	
	**Pulse Width Modulation**</a>

-   <a href="https://learn.sparkfun.com/tutorials/89">
	<figure markdown>
	Tutorial Thumbnail
	</figure>

	---
	
	**Analog vs. Digital**</a>

-   <a href="https://learn.sparkfun.com/tutorials/82">
	<figure markdown>
	Tutorial Thumbnail
	</figure>

	---
	
	**I2C**</a>

-   <a href="https://learn.sparkfun.com/tutorials/16">
	<figure markdown>
	Tutorial Thumbnail
	</figure>

	---
	
	**SPI**</a>

-   <a href="https://learn.sparkfun.com/tutorials/8">
	<figure markdown>
	Tutorial Thumbnail
	</figure>

	---
	
	**Serial Communication**</a>

-   <a href="https://learn.sparkfun.com/tutorials/5">
	<figure markdown>
	Tutorial Thumbnail
	</figure>

	---
	
	**How to Solder: Through-Hole Soldering**</a>

-   <a href="https://learn.sparkfun.com/tutorials/664">
	<figure markdown>
	Tutorial Thumbnail
	</figure>

	---
	
	**How to Work with Jumper Pads and PCB Traces**</a>

-   <a href="https://learn.sparkfun.com/tutorials/126">
	<figure markdown>
	Tutorial Thumbnail
	</figure>

	---
	
	**Motors and Selecting the Right One**</a>

-   <a href="https://learn.sparkfun.com/tutorials/115">
	<figure markdown>
	Tutorial Thumbnail
	</figure>

	---
	
	**Alternating Current (AC) vs. Direct Current (DC)**</a>

</div>

??? info "Need to control a different type of motor?"
	This tutorial is primarily focused on utilizing the TMC6300 motor driver to control a 3-phase brushless DC (BLDC) motor. We would recommend users explore other products for these specific motors and actuators. Below, are additional product tutorials and resources for our other actuator and motor types:

	=== "Brushed DC Motors"

		<div class="grid cards col-4" markdown align="center">

		-   <a href="https://learn.sparkfun.com/tutorials/934">
			<figure markdown>
			Tutorial Thumbnail
			</figure>

			---
			
			**Hookup Guide for the Qwiic Motor Driver**</a>

		-   <a href="https://learn.sparkfun.com/tutorials/526">
			<figure markdown>
			Tutorial Thumbnail
			</figure>

			---
			
			**TB6612FNG Hookup Guide**</a>
		
		</div>

	=== "Stepper Motors"

		<div class="grid cards col-4" markdown align="center">

		-   <a href="https://learn.sparkfun.com/tutorials/1200">
			<figure markdown>
			Tutorial Thumbnail
			</figure>

			---
			
			**SparkFun ProDriver Hookup Guide**</a>

		-   <a href="https://learn.sparkfun.com/tutorials/210">
			<figure markdown>
			Tutorial Thumbnail
			</figure>

			---
			
			**Easy Driver Hook-up Guide**</a>
		
		</div>

	=== "Servos"

		<div class="grid cards col-4" markdown align="center">

		-   <a href="https://learn.sparkfun.com/tutorials/1109">
			<figure markdown>
			Tutorial Thumbnail
			</figure>

			---
			
			**Basic Servo Control for Beginners**</a>

		-   <a href="https://learn.sparkfun.com/tutorials/526">
			<figure markdown>
			Tutorial Thumbnail
			</figure>

			---
			
			**Hobby Servo Tutorial**</a>
		
		-   <a href="https://learn.sparkfun.com/tutorials/910">
			<figure markdown>
			Tutorial Thumbnail
			</figure>

			---
			
			**Pi Servo pHAT (v2) Hookup Guide**</a>
		
		</div>

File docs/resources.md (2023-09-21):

## Product Resources

* :sfe-logo: [Product Page](https://www.sparkfun.com/products/22132)
* Component Documentation
	* :fontawesome-solid-file-pdf: [ESP32 Module Datasheet](./assets/component_documentation/esp32-wroom-32e_datasheet_en.pdf)
	* :fontawesome-solid-file-pdf: [TMC6300 Datasheet](./assets/component_documentation/TMC6300.pdf)
	* :fontawesome-solid-file-pdf: [TMAG5273 Datasheet](./assets/component_documentation/TMAG5273.pdf)
	* :fontawesome-solid-file-pdf: [INA240 Datasheet](./assets/component_documentation/INA240.pdf)
	* :fontawesome-solid-file-pdf: [WS2812 Datasheet](./assets/component_documentation/WS2812.pdf)
* :material-folder-cog: Design Files:
	* :fontawesome-solid-file-pdf: [Board Dimensions](./assets/board_files/dimensions.pdf)
	* :fontawesome-solid-file-pdf: [Schematic](./assets/board_files/schematic.pdf)
	* :material-folder-zip: [Eagle Files](./assets/board_files/eagle_files.zip)
* Arduino Library:
	* :material-github: [Simple FOC](https://github.com/simplefoc/Arduino-FOC)
	* :material-file-document-multiple: [Documentation](https://docs.simplefoc.com/)
		* [Installation](https://docs.simplefoc.com/library_download)
		* [Supported Hardware](https://docs.simplefoc.com/supported_hardware)
		* [Code Overview](https://docs.simplefoc.com/code)
* :material-youtube: [SFE Product Showcase](https://youtu.be/4GGIxnUDrU0)
* :material-github: [Hardware Repo](https://github.com/sparkfun/SparkFun_IoT_Brushless_Motor_Driver)

### Additional Resources

* [Motors and Motor Driver Product Category](https://www.sparkfun.com/categories/178)
* :material-account-supervisor: [SparkFun Technical Assistance](https://www.sparkfun.com/technical_assistance)

## 🏭&nbsp;Manufacturer's Resources
Analog Devices + Trinamic also provides great resources for the TMC6300 motor driver:

* [TMC6300 Product Page](https://www.trinamic.com/products/integrated-circuits/details/tmc6300-la/)
	* [Block Diagram/Pinout](https://www.trinamic.com/products/integrated-circuits/details/tmc6300-la/#block-diagram)
	* :material-file-document: [Datasheet](https://www.trinamic.com/products/integrated-circuits/details/tmc6300-la/#downloads-2)
	* :material-file-document-multiple: [Application Notes](https://www.trinamic.com/products/integrated-circuits/details/tmc6300-la/#downloads-1)
* :material-youtube: [Trinamic: TMC6300 Product Training Module](https://youtu.be/WCvQjW1gSNY)
* :material-head-question: [Technical Support Page](https://www.trinamic.com/support/technical-support/)

<center>
QR code to the hookup guide
</center>

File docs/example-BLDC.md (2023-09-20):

In this example, users will be utilizing the TMC6300 motor driver to spin the motor.

## Example Code
After installing and setting up the Arduino IDE and the Simple FOC Arduino library, users will need to upload the following example code using the **SparkFun ESP32 Thing Plus C** board definition. This code can be copied or downloaded below:

<center>
[:octicons-download-16:{ .heart } Download `BLDC.ino` Example Code](./assets/arduino_examples/BLDC/BLDC.ino){ .md-button .md-button--primary }
</center>

!!! code "Example Code"
	``` c++ title="BLDC.ino"
		--8<-- "./docs/assets/arduino_examples/BLDC/BLDC.ino"
	```

### Running the Motor
By default, the motor should spin automatically. However, if users wish to control the speed of the motor, they can uncomment lines **21-22** and **56-57** of code and reprogram the board.

??? code "Code Changes Highlighted"
	Uncomment the following lines of code (**21-22** and **56-57**):

	``` c++ hl_lines="21-22 56-57" title="BLDC.ino"
		--8<-- "./docs/assets/arduino_examples/BLDC/BLDC.ino"
	```

In order to drive the motor, users will need to access the [serial monitor](https://learn.sparkfun.com/tutorials/8) and provide the [commands](https://docs.simplefoc.com/commands_source) necessary to drive the motor. A full list of the available commands can be found in the [Simple FOC Arduino library documentation](https://docs.simplefoc.com/commands_source). However, only the `T` and `L` commands are enabled in the example code.

* Sending a `T` command will set the target motor velocity in rads/s
	* Example - Entering `T6` into the serial monitor, will set the target motor velocity to 6 radians/s.
* Sending a `L` command will set the voltage limit of the motor driver and in turn, the current limit *(voltage_limit / motor_resistance)*
	* Example - Entering `L5` into the serial monitor, will set the voltage limit to 5V and the current limit to .5A *(5V/10&ohm;)*.

!!! tip "Baud Rate"
	The serial monitor baud rate should be configured to `115200bps`.

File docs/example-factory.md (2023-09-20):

This example, allows users to reprogram their board with the same sketch that it comes pre-programmed with from SparkFun.

## Example Code
After installing and setting up the Arduino IDE and the Simple FOC Arduino library, users will need to upload the following example code using the **SparkFun ESP32 Thing Plus C** board definition. This code can be copied or downloaded below:

<center>
[:octicons-download-16:{ .heart } Download `IoT_MotorDriver.ino` Example Code](./assets/arduino_examples/IoT_MotorDriver/IoT_MotorDriver.ino){ .md-button .md-button--primary }
</center>

!!! code "Example Code"
	``` c++ title="IoT_MotorDriver.ino"
		--8<-- "./docs/assets/arduino_examples/IoT_MotorDriver/IoT_MotorDriver.ino"
	```

### Running the Motor
By default, the motor should be disabled and spin freely. Users can utilize the user buttons ++"13"++ and ++"14"++ to control the motor.

* ++"13"++ - Starts and stops the motor spin
* ++"14"++ - Reverses the direction of the motor's rotation, when it is spinning

!!! tip "Motor Overheating"
	When the motor is stopped, the motor driver is still enabled. Therefore, current is still running through the stator coils and holding the motor in place. After a few minutes, users may notice that the motor begins to heat up a bit.

	If this becomes an issue, users can modify their code to disable the motor driver when the motor stops. This will prevent the motor from heating up, but the motor will spin freely as the motor driver is no longer engaged.

	??? code "Modification"
		Modify the sketch and insert `motor.disable();` between lines `80` - `81`.

		``` c++ hl_lines="80 81" title="DC.ino"
			--8<-- "./docs/assets/arduino_examples/IoT_MotorDriver/IoT_MotorDriver.ino"
		```

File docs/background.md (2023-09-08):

---
icon: material/bookshelf
---

Below, are several articles, application notes, and other technical resources on 3-phase motors and utilizing a field-oriented control (FOC) scheme:

* Microchip Technology
	* [AN885: Brushless DC (BLDC) Motor Fundamentals](https://ww1.microchip.com/downloads/en/appnotes/00885a.pdf)
	* [AN2757: Sensored (Encoder-Based) Field-Oriented Control of Three-Phase Permanent Magnet Synchronous Motor (PMSM)](https://ww1.microchip.com/downloads/en/Appnotes/Sensored-Encoder-Based%29-Field-Oriented-Control-of-Three-Phase-%20Permanent-%20Magnet-%20Synchronous-DS00002757A.pdf)
	* [AN1078: Sensorless Field-Oriented Control of a PMSM](https://www.eeweb.com/wp-content/uploads/articles-app-notes-files-sensorless-field-oriented-control-of-a-pmsm-1340055193.pdf)
	* [AVR32723: Sensor Field-Oriented Control for Brushless DC motors with AT32UC3B0256](https://ww1.microchip.com/downloads/en/Appnotes/doc32126.pdf)
* Diodes Incorporated
	* [AN1164: Introduction to Brushless DC Motors](https://www.diodes.com/assets/Uploads/AN1164-BLDC-Motors.pdf)
* Monolithic Power Systems
	* [AN047: Brushless DC Motor Fundamentals](https://www.monolithicpower.com/media/document/Brushless_DC_Motor_Fundamentals.pdf)
* Texas Instruments
	* [Demystifying BLDC motor commutation: Trap, Sine, & FOC](https://www.ti.com/lit/ml/slyp711/slyp711.pdf)
	* [Sensored Field-Oriented Control of 3-Phase Permanent Magnet Synchronous Motors](https://www.ti.com/lit/an/sprabq2/sprabq2.pdf)
	* [Sensorless Field-Oriented Control of 3-Phase Permanent Magnet Synchronous Motors](https://www.ti.com/lit/an/sprabq3/sprabq3.pdf)
	* [Brushless-DC Motor Driver Considerations and Selection Guide](https://www.ti.com/lit/an/slvaes1a/slvaes1a.pdf)
	* [High-Performance Brushless DC Motor Control](https://www.ti.com/lit/an/sprt703/sprt703.pdf)
	* :material-video-box:&nbsp;[Field-oriented control of permanent magnet synchronous motors](https://www.ti.com/video/3881563245001)
	* :material-video-box:&nbsp;[Field-Oriented Control of Permanent Magnet Motors](https://www.ti.com/video/3871706529001)
		* :material-youtube:&nbsp;[Field-Oriented Control of Permanent Magnet Motors](https://www.youtube.com/watch?v=cdiZUszYLiA)
* MATLAB
	* :material-youtube:&nbsp;[Motor Control, Part 4: Understanding Field-Oriented Control](https://youtu.be/YPD1_rcXBIE)
* Analog Devices + Trinamic
	* [FOC As Hardware Building Block](https://www.trinamic.com/technology/motor-control-technology/field-oriented-control/)
* Infineon Technologies
	* [Motor Handbook](https://www.infineon.com/dgdl/Infineon-motorcontrol_handbook-AdditionalTechnicalInformation-v01_00-EN.pdf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)
	* [AN204469 - FM3 Family 3-Phase PMSM FOC Control](https://www.infineon.com/dgdl/Infineon-AN204469_FM3_Family_3_Phase_PMSM_FOC_Control-ApplicationNotes-v03_00-EN.pdf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)
	* [Block commutation vs. FOC in power tool motor control](https://www.infineon.com/dgdl/Infineon-Motor_power_tool_Block_Commutation_vs_FOC-ApplicationNotes-v01_00-EN.pdf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)
	* :material-presentation-play:&nbsp;[Motor control for BLDC: block commutation vs. field-oriented control](https://www.infineon.com/cms/media/eLearning/PSS/PSS_eLearning_Motor_control_for_BLDC_in_low_voltage_drives_english/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)
* ST Microelectronics
	* [AN5397: Current Sensing in Motion Control Applications](https://www.st.com/resource/en/application_note/an5397-current-sensing-in-motion-control-applications-stmicroelectronics.pdf)
	* [AN4220: Sensorless Six-Step BLDC Commutation](https://www.st.com/resource/en/application_note/an4220-sensorless-sixstep-bldc-commutation-stmicroelectronics.pdf)

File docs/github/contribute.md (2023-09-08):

# Contribute: Make an Augmentation!
Spot an improvement opportunity? Feel free to contribute to our open-source design and documentation. 

## :material-file-document-multiple:&nbsp;Improve our Documentation
All of this documentation can be modified by you! Please help us make it better.

* These pages are contained in the [`docs` folder](https://github.com/sparkfun/SparkFun_IoT_Brushless_Motor_Driver/tree/main/docs) of the [SparkFun IoT Brushless Motor Driver repository](https://github.com/sparkfun/SparkFun_IoT_Brushless_Motor_Driver).

<!-- ### :material-source-pull:&nbsp;Submit a Correction -->
### Submit a Correction

1. With a GitHub account, [fork this repository](https://github.com/sparkfun/SparkFun_IoT_Brushless_Motor_Driver/fork).
2. Add your corrections or improvements to the markdown file.
3. File a pull request with your changes, and enjoy making the ~~words~~ ~~worlds~~ world a better place.
	* Once received, the documentation specialist will automatically be notified.
	* We will review your suggested improvements to make sure they are correct and fit within our documentation standards.

## :material-cog:&nbsp;Improve our Hardware Design
All of our designs are open-source! Please help us make it better.

* Our board design files are contained in the [`Hardware` folder](https://github.com/sparkfun/SparkFun_IoT_Brushless_Motor_Driver/tree/main/Hardware) of the [SparkFun IoT Brushless Motor Driver repository](https://github.com/sparkfun/SparkFun_IoT_Brushless_Motor_Driver).

<!-- ### :material-source-pull:&nbsp;Submit a Design Enhancement -->
### Submit a Design Enhancement

1. With a GitHub account, [fork this repository](https://github.com/sparkfun/SparkFun_IoT_Brushless_Motor_Driver/fork).
2. Add your design augmentation(s)
3. File a pull request with your changes, and enjoy making the ~~words~~ ~~worlds~~ world a better place.
	1. Once received, the engineer in charge of the original design will automatically be notified.
	2. We will review your suggested improvement(s) to verify that they are within our board design standards and meet our product design requirements.
	3. If approved, we will flag these changes for our next board revision. Congrats! 🍻

		!!! info
			Even if your suggestion is accepted, these changes may not be immediately available for purchase. We may have to cycle through our current product inventory first.

## Contributors&nbsp;:clap:
Let's provide some recognition to the contributors for this project!

GitHub Contributors Image
<br>


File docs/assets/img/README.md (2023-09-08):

img directory
====================
This folder should contain the images for the product documentation

## General Images
* `sfe_logo_sm.png` - SparkFun flame logo (Cover page for with-pdf extension)
* `sfe_logo_sq.png` - SparkFun flame logo (favicon)

## Directory
* `hookup_guide` - Images for the hookup guide pages

## QR Codes
* [QR code generator](https://qrgenerator.org/)
	* Flame Color: #E0311D
	* Frame Color: #3C464D
* [Remove meta data from svg](https://jakearchibald.github.io/svgomg/)

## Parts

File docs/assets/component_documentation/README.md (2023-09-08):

component_documentation directory
====================

A copy of the datasheets, user manuals, programming guides, etc. of the major electrical components on the board.

* [APA2112 Datasheet](AP2112.pdf) (PDF)
* [APA63357 Datasheet](AP63356-AP63357.pdf) (PDF)
* [CH340C Datasheet](CH340DS1.PDF) (PDF)
* [ESP32-WROOM Datasheet](esp32-wroom-32e_datasheet_en.pdf) (PDF)
* [TMC6300 Datasheet](TMC6300.pdf) (PDF)
* [TMAG5273 Datasheet](TMAG5273.pdf) (PDF)
* [INA240 Datasheet](INA240.pdf) (PDF)
* [MCP6021 Datasheet](MCP6021.pdf) (PDF)
* [WS2812 Datasheet](WS2812.pdf) (PDF)

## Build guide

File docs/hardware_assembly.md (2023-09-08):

---
icon: material/tools
---

## USB Programming
The USB connection is utilized for programming and serial communication. Users only need to plug their IoT Motor Driver into a computer using a USB-C cable.

<figure markdown>
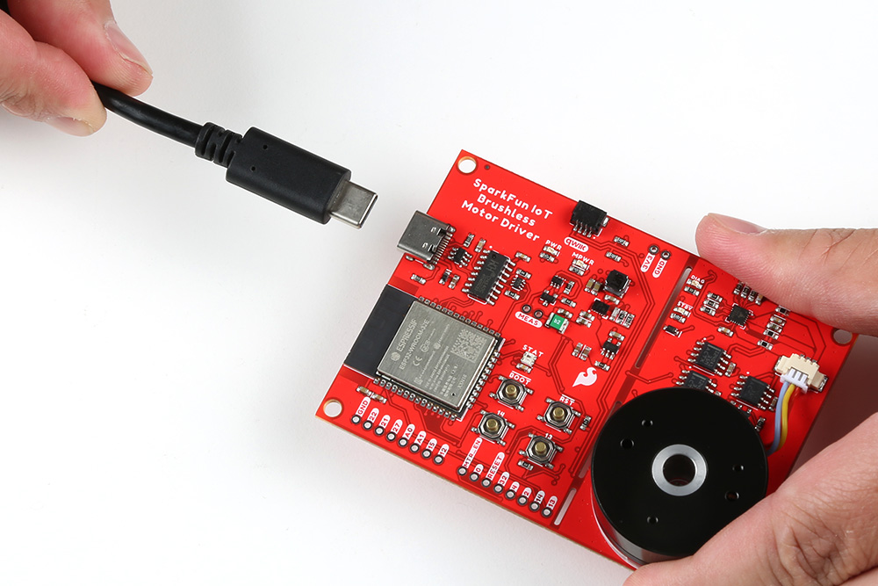
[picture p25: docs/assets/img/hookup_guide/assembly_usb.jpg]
IoT Motor Driver USB connection

<figcaption markdown>The IoT Motor Driver with USB-C cable attached.</figcaption>
</figure>

## Headers
??? note "New to soldering?"
	If you have never soldered before or need a quick refresher, check out our [How to Solder: Through-Hole Soldering](https://learn.sparkfun.com/tutorials/how-to-solder-through-hole-soldering) guide.

	<div class="grid cards col-4" markdown  align="center">

	-   <a href="https://learn.sparkfun.com/tutorials/5">
		<figure markdown>
		Tutorial thumbnail
		</figure>

		---
		
		**How to Solder: Through-Hole Soldering**</a>

	</div>

The pins for the IoT Motor Driver are broken out into 0.1"-spaced pins on the outer edges of the board. When selecting headers, be sure you are aware of the functionality you require.

<figure markdown>
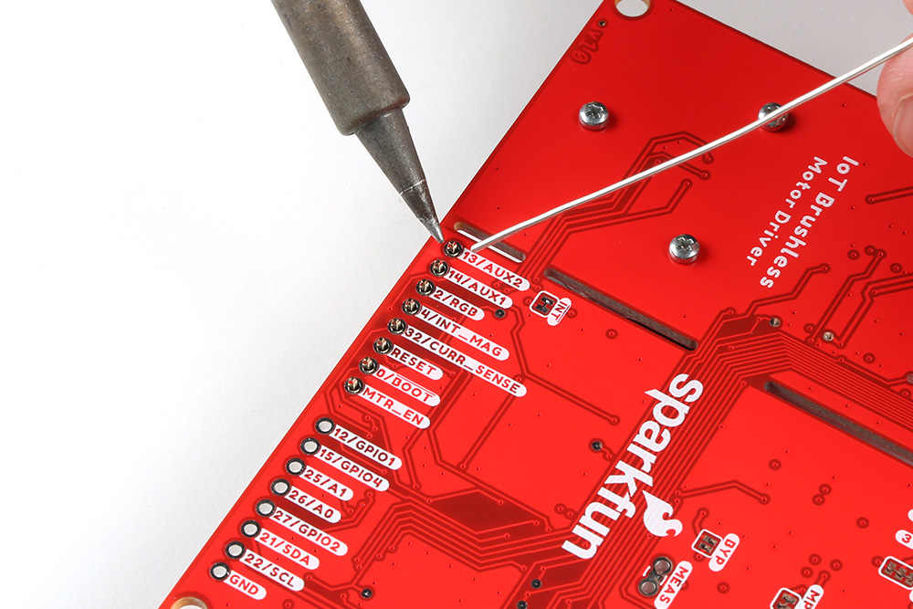
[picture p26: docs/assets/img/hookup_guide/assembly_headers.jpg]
Soldering headers

<figcaption markdown>Soldering headers to the IoT Motor Driver.</figcaption>
</figure>

### Qwiic Devices
The Qwiic system allows users to effortlessly prototype with a Qwiic compatible I<sup>2</sup>C device without soldering. Users can attach any Qwiic compatible [sensor or board](https://www.sparkfun.com/qwiic#sensors), with just a [Qwiic cable](https://www.sparkfun.com/products/15081). (*\*The example below, is for demonstration purposes and is not pertinent to the board functionality or this tutorial.*)

<figure markdown>
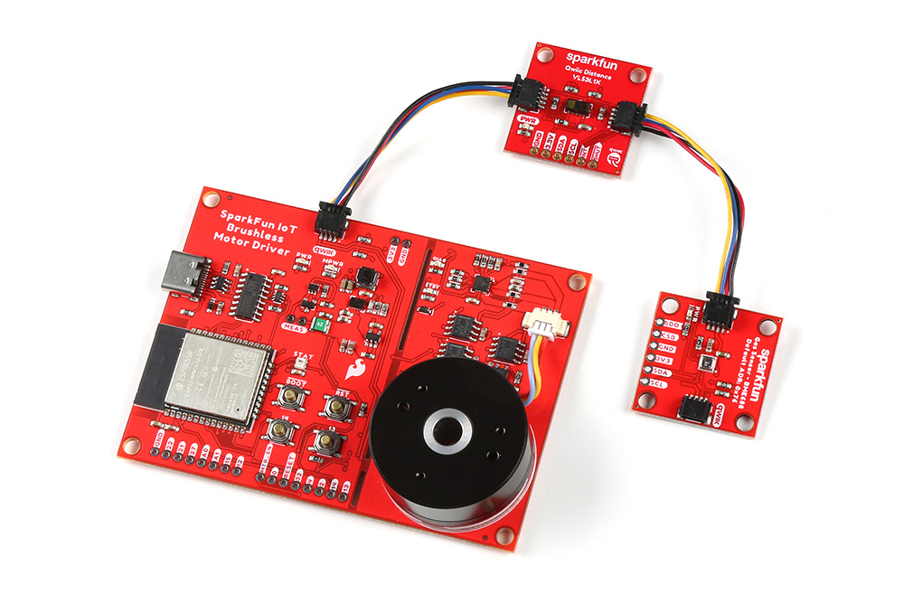
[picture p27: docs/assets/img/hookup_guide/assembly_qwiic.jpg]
Qwiic devices connected to IoT Motor Driver

<figcaption markdown>The [BME688 environmental](https://www.sparkfun.com/products/19096) and [VL53L1X distance](https://www.sparkfun.com/products/14722) Qwiic sensor boards connected to the IoT Motor Driver.</figcaption>
</figure>

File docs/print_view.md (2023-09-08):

---
hide:
  - navigation
  - toc
icon: material/printer
---

--8<-- "./docs/introduction.md:5"

# Hardware Overview
--8<-- "./docs/hardware_overview.md:5"

# Hardware Assembly
--8<-- "./docs/hardware_assembly.md:5"

# Software Overview
--8<-- "./docs/software_overview.md:5"

## Example - BLDC
--8<-- "./docs/example-BLDC.md"

## Example - FOC Algorithm
--8<-- "./docs/example-FOC.md"

## Example - Factory Reset
--8<-- "./docs/example-factory.md"

# Troubleshooting Tips
--8<-- "./docs/troubleshooting_tips.md:5"

# Resources:
--8<-- "./docs/resources.md"

## Background Resources
--8<-- "./docs/background.md:5"

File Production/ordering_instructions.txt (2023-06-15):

panel size, 193x137mm
PCB thickness, 1.6mm
number of layers, 4
soldermask color, Red
silkscreen color, White
oz copper, 1oz
finish, HASL lead free
stencils, top
pcs per panel, 4
min trace width, 0.1313mm / 0.0052in
min drill size, 0.3048mm / 0.0120in

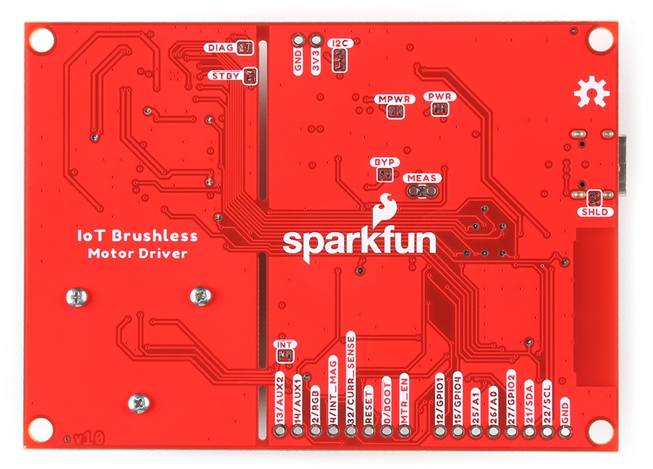
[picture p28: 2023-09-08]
docs/assets/img/hookup_guide/bottom.jpg

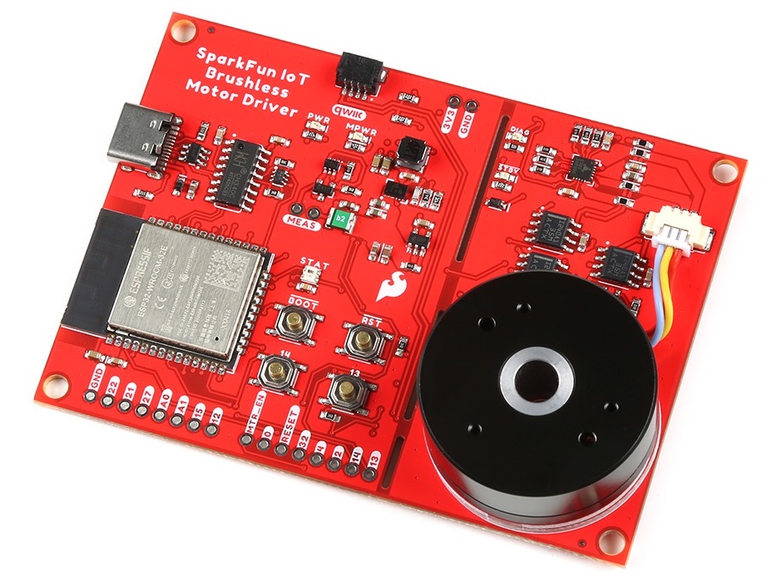
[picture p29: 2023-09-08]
docs/assets/img/hookup_guide/thumbnail.jpg

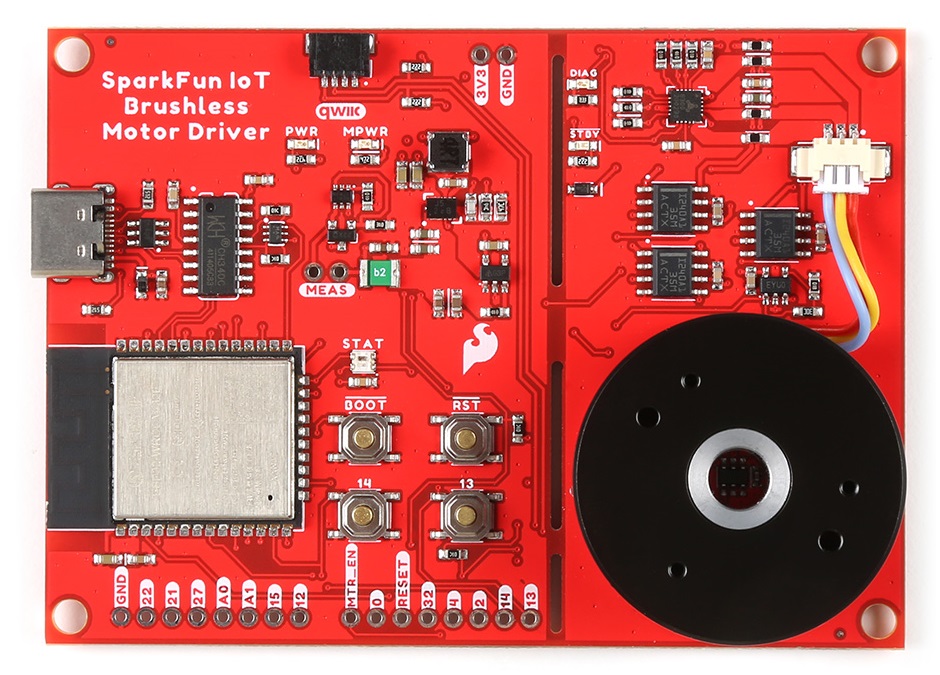
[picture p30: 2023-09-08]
docs/assets/img/hookup_guide/top.jpg

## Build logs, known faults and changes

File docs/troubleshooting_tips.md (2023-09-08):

---
icon: sfe-logo
---

!!! warning "Need Help?"
	If you need technical assistance or more information on a product that is not working as you expected, we recommend heading on over to the [SparkFun Technical Assistance](https://www.sparkfun.com/technical_assistanc) page for some initial troubleshooting.

	<center>
	[SparkFun Technical Assistance Page](https://www.sparkfun.com/technical_assistance){ .md-button .md-button--primary }
	</center>
	
	If you can't find what you need there, the [SparkFun Forums](https://forum.sparkfun.com/index.php) is a great place to search product forums and ask questions.
	
	!!! info "Account Registration Required"
		If this is your first visit to our forum, you'll need to create a [Forum Account](https://forum.sparkfun.com/ucp.php?mode=register) to post questions.

## ESP32 Compile Error
If users run into an error similar to, `fatal error: soc/soc_caps.h: No such file or directory`, it may be due to an issue with the version of the ESP32 Arduino core that is installed in the **Boards Manager**. Users should make sure the have the latest version of the ESP32 Arduino core installed; or at least a version later than `v2.0.1`.

!!! info
	For more information, please reference this [forum post](https://community.simplefoc.com/t/compilation-error/1700) for the Simple FOC Arduino library.

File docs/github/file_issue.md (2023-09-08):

# Did we make a mistake?

Spot something wrong? Please let us know. 

<!-- Technical Assistance Box -->
!!! warning "Need Help?"
	If you need technical assistance or more information on a product that is not working as you expected, we recommend heading on over to the [SparkFun Technical Assistance](https://www.sparkfun.com/technical_assistanc) page for some initial troubleshooting. This **Submit Issues** page is not where users should seek assistance.

	<center>
	[SparkFun Technical Assistance Page](https://www.sparkfun.com/technical_assistance){ .md-button .md-button--primary }
	</center>
	
	If you can't find what you need there, the [SparkFun Forums](https://forum.sparkfun.com/index.php) is a great place to search the product forums and ask questions.
	
	!!! info "Account Registration Required"
		For your first visit to our forum, you'll need to create a [Forum Account](https://forum.sparkfun.com/ucp.php?mode=register) to post questions.

## Discrepancies in the Documentation

All of our documentation can be modified by you! Please help us make it better.

* The documentation files for these pages are contained in the [`docs` folder](https://github.com/sparkfun/SparkFun_IoT_Brushless_Motor_Driver/tree/main/docs) of the [SparkFun IoT Brushless Motor Driver repository](https://github.com/sparkfun/SparkFun_IoT_Brushless_Motor_Driver).

### 🔍 Spot something wrong?

If a section of the documentation is incorrect, please [open an issue](https://github.com/sparkfun/SparkFun_IoT_Brushless_Motor_Driver/issues) and let us know.

### Do you have a suggested correction?

1. With a GitHub account, [fork this repository](https://github.com/sparkfun/SparkFun_IoT_Brushless_Motor_Driver/fork).
2. Add your correction(s) or improvement(s) to the markdown file(s)
3. File a pull request with your changes, and enjoy making the ~~words~~ ~~worlds~~ world a better place.
	* Once received, the documentation specialist will automatically be notified.
	* We will review your suggested improvement(s) to make sure they are correct and fit within our documentation standards.

## Problems in the Hardware Design

All of our designs are open-source! Please help us make it better.

* Our board design files are contained in the [`Hardware` folder](https://github.com/sparkfun/SparkFun_IoT_Brushless_Motor_Driver/tree/main/Hardware) of the [SparkFun IoT Brushless Motor Driver repository](https://github.com/sparkfun/SparkFun_IoT_Brushless_Motor_Driver).

### Does something not make sense? 🤔

If part of the design is confusing, please [open an issue](https://github.com/sparkfun/SparkFun_IoT_Brushless_Motor_Driver/issues) and let us know.

### Did we forget to include an important function of the board? 🤦

If part of the board's functionality is missing, please [open an issue](https://github.com/sparkfun/SparkFun_IoT_Brushless_Motor_Driver/issues) and file a feature request.

!!! tip "Design Considerations"
	Please keep in mind that we may intentionally exclude certain functions of the board to meet our product design requirements.
	
	* *For example, our Qwiic Micro boards are intended to fit on a small board layout and only use I<sup>2</sup>C communication; therefore, we may not have the SPI and interrupt pins available for users.*

### Do you wish to contribute directly to improving the board design?

1. With a GitHub account, [fork this repository](https://github.com/sparkfun/SparkFun_IoT_Brushless_Motor_Driver/fork).
2. Add your design augmentation(s)
3. File a pull request with your changes, and enjoy making the ~~words~~ ~~worlds~~ world a better place.
	1. Once received, the engineer in charge of the original design will automatically be notified.
	2. We will review your suggested improvement(s) to verify that they are within our board design standards and meet our product design requirements.
	3. If approved, we will flag these changes for our next board revision. Congrats! 🍻

		!!! info
			Even if your suggestion is accepted, these changes may not be immediately available for purchase. We may have to cycle through our current product inventory first.

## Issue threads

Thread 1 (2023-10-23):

Is there an example for simplefoc angle controlling?

chengyingyuan, 2023-10-23:
I tried motor driver using Arduino simplefoc. When I set control type to  "velocity openloop" or "angle openloop", it runs well. But for "velocity" and "angle" type, the motor cannot go to the set point. It spins cw then ccw then cw again and again.

The motor and driver I used is SparkFun IoT Brushless Motor Driver v10.  I connect it to mac pro m2 and don't change anything(all as factory setting).

I created an arduino sketch, set "SparkFun ESP32 Thing Plus C" as board type. The source code as following.

`
#include <Wire.h>
#include <SimpleFOC.h>
#include <SparkFun_TMAG5273_Arduino_Library.h>

#define RAD2DEGREES(v) ((v * 4068) / 71)
#define DEG2RADIANS(v) ((v * 71) / 4068)

//GPIO
#define auxBtn2   13
#define auxBtn1   14

//driver
#define uh16      16
#define ul17      17
#define vh18      18
#define wh19      19
#define vl23      23
#define wl33      33
#define diag      34 // <-TMC6300
#define vio       05 // ->TMC6300, reset to standby(low)/enable(high)
#define i2cint    04 // <-TMAG5273
#define i2cscl    22 // <-TMAG5273
#define i2csda    21 // <-TMAG5273
#define i2caddr   TMAG5273_I2C_ADDRESS_INITIAL
#define rgbLED    02 // ->WS2812
#define curSense  32 // <-MCP6021
#define curSenseU 35 // <-INA240
#define curSenseV 36 // <-INA240
#define curSenseW 39 // <-INA240

// I2C default address
uint8_t i2cAddress = TMAG5273_I2C_ADDRESS_INITIAL;
// Set constants for setting up device
uint8_t conversionAverage = TMAG5273_X32_CONVERSION;
uint8_t magneticChannel = TMAG5273_XYX_ENABLE;
uint8_t angleCalculation = TMAG5273_XY_ANGLE_CALCULATION;
float angleCalculationVal = 0;
TMAG5273 _sensor;  // Initialize hall-effect sensor

void initMySensorCallback(){
  // do the init
}

float readMySensorCallback(){
  if((_sensor.getMagneticChannel() != 0) && (_sensor.getAngleEn() != 0)) // Checks if mag channels are on - turns on in setup
  {
    angleCalculationVal = _sensor.getAngleResult();
    //sensor.update();
  }
  else
  {
    Serial.println("Mag Channels disabled, stopping..");
    while(1);
  }

  return DEG2RADIANS(angleCalculationVal);
}

GenericSensor sensor = GenericSensor(readMySensorCallback, initMySensorCallback);

// inline current sensor instance
// InlineCurrentSense(float shunt_resistor, float gain, int pinA, int pinB, int pinC = NOT_SET)
InlineCurrentSense current_sense = InlineCurrentSense((float)0.01, (float)20.0, curSenseU, curSenseV, curSenseW);

// BLDC motor & driver instance
// BLDCMotor motor = BLDCMotor(pole pair number);
BLDCMotor motor = BLDCMotor(7); // BLDCMotor(11, 10.5, 120)
// BLDCDriver3PWM driver = BLDCDriver3PWM(pwmA, pwmB, pwmC, Enable(optional));
BLDCDriver6PWM driver = BLDCDriver6PWM(uh16, ul17, vh18, vl23, wh19, wl33);

static float zero_rad = 0.0;

// instantiate the commander
Commander command = Commander(Serial);
void doTarget(char* cmd) { command.scalar(&motor.target, cmd); }
void doLimit(char* cmd) { command.scalar(&motor.voltage_limit, cmd); }
void doVelocity(char* cmd) { command.scalar(&motor.velocity_limit, cmd); }
void doMotor(char* cmd){ command.motor(&motor, cmd); }
void doStop(char* cmd) { motor.target = motor.shaft_angle; }
void doZero(char* cmd) { zero_rad = sensor.getAngle(); motor.sensor_offset = 0; motor.shaft_angle = 0; }

struct Button{
  const uint8_t PIN;
  uint32_t numberKeyPresses;
  bool pressed;
};
Button aux1 = {auxBtn1, 0, false};
Button aux2 = {auxBtn2, 0, false};

void IRAM_ATTR isrbtn1(){
  aux1.pressed = true;
  //target_velocity = target_velocity*(-1);
  Serial.println("Changing directions.. ");
}

void IRAM_ATTR isrbtn2(){
  aux2.numberKeyPresses++;
  aux2.pressed = true;

  if((aux2.numberKeyPresses % 2) == 0)
  {
    //target_velocity = 0;
    //motor.disable();
    Serial.println("Stopping motor.. ");
  }
  else
  {
    //target_velocity = 5;
    //motor.enable();
    Serial.println("Starting motor.. ");
  }
}

void setup() {
  // configure i2C hall sensor
  //Wire.setClock(400000);
  //Wire.setPins(18, 19);
  Wire.begin();
  Serial.begin(115200);

  pinMode(aux1.PIN, INPUT_PULLUP); // Sets pin 14 on the ESP32 as an interrupt
  attachInterrupt(aux1.PIN, isrbtn1, FALLING); // Triggers when aux1 is pulled to GND (button pressed)
  pinMode(aux2.PIN, INPUT_PULLUP); // Sets pin 13 on the ESP32 as an interrupt
  attachInterrupt(aux2.PIN, isrbtn2, FALLING); // Triggers when aux2 is pulled to GND (button pressed)

  // If begin is successful (0), then start example
  if(_sensor.begin(i2cAddress, Wire) == true) {
    //Serial.println("Begin");
  }
  else { // Otherwise, infinite loop
    Serial.println("Hall sensor failed to setup - Freezing code.");
    while(1); // Runs forever
  }
  // Set the device at 32x average mode
  _sensor.setConvAvg(conversionAverage);
  // Choose new angle to calculate from
  // Can calculate angles between XYX, YXY, YZY, and XZX
  _sensor.setMagneticChannel(magneticChannel);
  // Enable the angle calculation register
  // Can choose between XY, YZ, or XZ priority
  _sensor.setAngleEn(angleCalculation);
  // initialise magnetic sensor hardware
  sensor.init();
  motor.linkSensor(&sensor);

  // driver config
  // power supply voltage [V]
  driver.voltage_power_supply = 3.3;
  driver.pwm_frequency = 20000;
  driver.voltage_limit = 4;
  // limit the maximal dc voltage the driver can set
  // as a protection measure for the low-resistance motors
  // this value is fixed on startup
  //driver.voltage_limit = 6;
  driver.init();
  // link current sense and driver
  current_sense.linkDriver(&driver);
  // link the motor and the driver
  motor.linkDriver(&driver);

  // limiting motor movements
  // limit the voltage to be set to the motor
  // start very low for high resistance motors
  // currnet = resistance*voltage, so try to be well under 1Amp
  //motor.voltage_limit = 3;   // [V]
  // limit/set the velocity of the transition in between
  // target angles
  //motor.velocity_limit = 5; // [rad/s] cca 50rpm

  // set control loop type to be used
  motor.torque_controller = TorqueControlType::foc_current;
  //motor.controller = MotionControlType::angle;
  motor.controller = MotionControlType::velocity;

  // controller configuration based on the control type
  motor.PID_velocity.P = 0.05;
  motor.PID_velocity.I = 1;
  motor.PID_velocity.D = 0;
  // default voltage_power_supply
  motor.voltage_limit = 4;

  // velocity low pass filtering time constant
  motor.LPF_velocity.Tf = 0.01;

  // angle loop controller
  motor.P_angle.P = 20;
  // angle loop velocity limit
  motor.velocity_limit = 20;

  // add current limit
  // motor.phase_resistance = 3.52 // [Ohm]
  // motor.current_limit = 2;   // [Amps] - if phase resistance defined

// comment out if not needed
  motor.useMonitoring(Serial);
  motor.monitor_downsample = 0; // // initially disable the real-time monitor //100; // set downsampling can be even more > 100
  //motor.monitor_variables = _MON_CURR_Q | _MON_CURR_D; // set monitoring of d and q currents

  motor.init();

  // current sense init hardware
  current_sense.init();
  // link the current sense to the motor
  motor.linkCurrentSense(&current_sense);

  // invert phase b gain
  //current_sense.gain_b *=-1;
  // skip alignment
  //current_sense.skip_align = true;

  // align sensor and start FOC
  motor.initFOC();

  // set the initial motor target
  // motor.target = 0.2; // Amps - if phase resistance defined
  motor.target = 0; // Volts

  // add target command T
  // command.add('T', doTarget, "target current"); // - if phase resistance defined
  //command.add('T', doTarget, "target voltage");
  command.add('M', doMotor, "motor control");
  command.add('S', doStop, "stop motor");
  command.add('Z', doZero, "set zero");
  //command.add('L', doLimit, "voltage limit");
  //command.add('V', doVelocity, "movement velocity");
  //command.verbose = VerboseMode::nothing; // disable commander output to serial

  Serial.println(F("Motor ready."));
  Serial.println(F("Set the target using serial terminal:"));
  _delay(1000);
}

void loop() {

  // Button Press ISR
  if(aux1.pressed){
    aux1.pressed = false;
  }

  // Turning motor on and off
  if(aux2.pressed){
    aux2.pressed = false;
  }

  // main FOC algorithm function
  motor.loopFOC();

  // Motion control function
  motor.move();

  // display the currents
  motor.monitor();
  // user communication
  command.run();
}

`

The esp32(by Espressif Systems) version is 2.0.14, and simplefoc version is 2.3.1.  I tried a whole day to adjust luxuriant PID settings using simplefoc studio (I forked one to make it work with macOS m1/m2 natively, https://github.com/chengyingyuan/SimpleFOCStudio) without success.

Are there any hints?

Hiren017, 2024-10-04:
Here you go:

#include <Wire.h>
#include <SparkFun_TMAG5273_Arduino_Library.h>
#include <SimpleFOC.h>

#define UH 16
#define UL 17
#define VH 18
#define VL 23
#define WH 19
#define WL 33

BLDCMotor motor = BLDCMotor(7);
BLDCDriver6PWM driver = BLDCDriver6PWM(UH, UL, VH, VL, WH, WL);

class TMAG5273_Sensor : public Sensor {
public:
  TMAG5273_Sensor(TMAG5273* sensor)
    : tmag_sensor(sensor) {}

  float getSensorAngle() override {
    // Get the angle from the TMAG5273 sensor and convert to radians
    float angle_deg = tmag_sensor->getAngleResult();  // Get angle in degrees
    return (angle_deg * PI) / 180.0;                  // Convert degrees to radians
  }

private:
  TMAG5273* tmag_sensor;
};

TMAG5273 sensor;
TMAG5273_Sensor tmag_sensor_wrapper(&sensor);

unsigned long previousMillis = 0;
const long interval = 1000;

uint16_t position_count = 0;

float target_angle_deg = 0.0;
float target_angle_rad = 0.0;
float current_angle = 0.0;

// I2C default address
uint8_t i2cAddress = TMAG5273_I2C_ADDRESS_INITIAL;

// Set constants for setting up device
uint8_t conversionAverage = TMAG5273_X32_CONVERSION;
uint8_t magneticChannel = TMAG5273_XYX_ENABLE;
uint8_t angleCalculation = TMAG5273_XY_ANGLE_CALCULATION;

bool dataread = false;

void readsensor(void) {
  if ((sensor.getMagneticChannel() != 0) && (sensor.getAngleEn() != 0))  // Checks if mag channels are on - turns on in setup
  {
    current_angle = sensor.getAngleResult();
    Serial.printf("current position : %0.2f°\n", current_angle);
  } else {
    Serial.println("Mag Channels disabled, stopping..");
    while (1);
  }
}

void setup() {
  Wire.begin();
  // Start serial communication at 115200 baud
  Serial.begin(115200);
  delay(2000);
  if (sensor.begin(i2cAddress, Wire) == true) {
    Serial.println("Begin");
  } else {
    Serial.println("Device failed to setup - Freezing code.");
    while (1)
      ;
  }

  sensor.setConvAvg(conversionAverage);
  sensor.setMagneticChannel(magneticChannel);
  sensor.setAngleEn(angleCalculation);

  driver.voltage_power_supply = 5.0;
  driver.pwm_frequency = 32000;
  driver.voltage_limit = 11.0;
  driver.init();
  motor.linkSensor(&tmag_sensor_wrapper);
  motor.linkDriver(&driver);
  motor.voltage_limit = 7.4;
  motor.velocity_limit = 10.0;
  motor.controller = MotionControlType::angle;
  motor.PID_velocity.P = 0.005f;
  motor.PID_velocity.I = 0.5;
  motor.PID_velocity.D = 0;
  motor.PID_velocity.output_ramp = 1000;
  motor.LPF_velocity.Tf = 0.01f;
  motor.P_angle.P = 20;
  motor.init();
  motor.initFOC();
  motor.enable();
}

void loop() {

  if (Serial.available() > 0) {
    String inputString = Serial.readStringUntil('\n');
    target_angle_deg = inputString.toFloat();
    target_angle_rad = ((target_angle_deg * PI) / 180.0) * (-1);
    Serial.printf("Target Angle value = %0.2f°\n", target_angle_deg);
    Serial.flush();
  }

  unsigned long currentMillis = millis();

  if (currentMillis - previousMillis >= interval) {
    previousMillis = currentMillis;
    readsensor();
  }

  motor.loopFOC();
  motor.move(target_angle_rad);
}

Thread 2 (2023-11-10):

error: 'mcpwm_isr_register' was not declared in this scope

lboue, 2023-11-10:
### Subject of the issue

    error: 'mcpwm_isr_register' was not declared in this scope

### Your workbench
Arduino IDE Version: 2.2.1

### Steps to reproduce
How to reproduce this issue :
 * Build [arduino_examples/BLDC/BLDC.ino](https://github.com/sparkfun/SparkFun_IoT_Brushless_Motor_Driver/blob/main/docs/assets/arduino_examples/BLDC/BLDC.ino)

### Expected behavior
It should with

### Actual behavior
This error:

    In file included from c:\Arduino\libraries\Simple_FOC\src\current_sense\hardware_specific\esp32\esp32_mcu.cpp:3:
    c:\users\ludovic\downloads\rf433\libraries\simple_foc\src\drivers\hardware_specific\esp32\esp32_driver_mcpwm.h:11:62: note: '#pragma message: SimpleFOC: compiling for ESP32 MCPWM driver'
       11 | #pragma message("SimpleFOC: compiling for ESP32 MCPWM driver")
          |                                                              ^
    c:\Arduino\libraries\Simple_FOC\src\current_sense\hardware_specific\esp32\esp32_mcu.cpp: In function 'void _driverSyncLowSide(void*, void*)':
    c:\Arduino\libraries\Simple_FOC\src\current_sense\hardware_specific\esp32\esp32_mcu.cpp:119:5: error: 'mcpwm_isr_register' was not declared in this scope
      119 |     mcpwm_isr_register(mcpwm_unit, mcpwm0_isr_handler, NULL, ESP_INTR_FLAG_IRAM, NULL);  //Set ISR Handler
          |     ^~~~~~~~~~~~~~~~~~
    c:\Arduino\libraries\Simple_FOC\src\current_sense\hardware_specific\esp32\esp32_mcu.cpp:121:5: error: 'mcpwm_isr_register' was not declared in this scope
      121 |     mcpwm_isr_register(mcpwm_unit, mcpwm1_isr_handler, NULL, ESP_INTR_FLAG_IRAM, NULL);  //Set ISR Handler
          |     ^~~~~~~~~~~~~~~~~~

    exit status 1

    Compilation error: exit status 1

UliBartels, 2024-02-01:
Hey Iboue,

I recently solved the same issue on my system and I don't think this is an issue with the SimpleFOC library but rather your esp32 setup. Take a look in your board manager and check which version of the esp32 board library you have installed. For me, it turned out I had 3.0.0.alpha. Reason for this was that in my package manager I had:

https://raw.githubusercontent.com/espressif/arduino-esp32/gh-pages/package_esp32_dev_index.json

rather than:

https://raw.githubusercontent.com/espressif/arduino-esp32/gh-pages/package_esp32_index.json

I uninstalled esp32, switched the package link from dev branch to the actual esp32 branch and installed esp32 version 2.0.14. This fixed the issue.

lboue, 2024-02-01:
Thanks @UliBartels

Closed 2024-02-01.

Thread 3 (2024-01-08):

Closed Loop Control - TMAG5273 to simpleFOC hallsensor.h & INA240 & MPC6021 to simpleFOC InlineCurrentSense.h

aiaaaa, 2024-01-08:
Greetings, happy new year, and hope all is well! I am really learning a lot from this board and my deep dive with it, it’s been a wonderful introduction into the world of motors and FOC control.

I have a beginner question, and basically was wondering are there any examples or hints you could give for closed loop controls for this board? It works very well as a wheel for IoT control, but I was hoping to implement it as a motor as opposed to a potentiometer. Hoping to implement very smooth rotation (as opposed to direct voltage open control), haptics, gimbal style motion and anything else. I am new to motor control and a bit new to coding. I could use some pointing in the right direction or som bread crumbs, as it seems. I tried to create a script that calculated RPM and velocity from the angle data from

Specifically can you help find the output of SparkFun_TMAG5273_Arduino_Library_Defs.h, that might “fit” in the HallSensor.h of simpleFOC, and can you help find the INA240/MPC6021 outputs that would match the InlineCurrentSense.h of simpleFOC, either of these would close the loop and get smooth motor operation:

(1) the output of the TMAG5273 chip is not the same as the simpleFOC hallsensor.h input.

- simpleFOC required input for HallSensor:

class HallSensor: public Sensor{
 public:
    /**
    HallSensor class constructor
    @param encA  HallSensor A pin
    @param encB  HallSensor B pin
    @param encC  HallSensor C pin
    @param pp  pole pairs  (e.g hoverboard motor has 15pp and small gimbals often have 7pp)
    @param index index pin number (optional input)
    */
    HallSensor(int encA, int encB, int encC, int pp);

- TMAG5273 Output:

All enumerators from class: SparkFun_TMAG5273_Arduino_Library_Defs.h

(2) And the output of the INA240 & MPC6021 are not the same as the simpleFOC InlineCurrentSense.h input:

- simpleFOC required input for InlineCurrentSense.h:

class InlineCurrentSense: public CurrentSense{
  public:
    /**
      InlineCurrentSense class constructor
      @param shunt_resistor shunt resistor value
      @param gain current-sense op-amp gain
      @param phA A phase adc pin
      @param phB B phase adc pin
      @param phC C phase adc pin (optional)
    */

- INA240 Current-Sense Amplifier and MPC6221 OpAmp outputs per the manual:
INA240 (U) on GPIO 35, INA240 (V) on GPIO 36, INA240 (W) on GPIO 39, MCP6021 on GPIO 32

### Subject of the issue
Using either of the two closed loop FOC control:
TMAG5273 to simpleFOC hallsensor.h & INA240 & MPC6021 to simpleFOC InlineCurrentSense.h

### Your workbench
* What development board or microcontroller are you using?
Only using the included board:
[SparkFun_IoT_Brushless_Motor_Driver]
* What version of hardware or breakout board are you using?
Revision number listed on bottom left of back red board, v10 (cannot see a . could be v1.0 but reads as v10)
* How is the breakout board wired to your microcontroller?
NA
* How is everything being powered?
USB over Battery, or USB over computer (both utilized)
* Are there any additional details that may help us help you?
No, stock all in one board configuration.

### Steps to reproduce
Issue here is in generating the code to begin with, see above description

### Expected behavior
 simpleFOC hallsensor.h should be populated with data from TMAG5273 hall sensor
 simpleFOC InlineCurrentSense.h should be populated with data from INA240 & MPC6021

### Actual behavior

Currently TMAG5273 hall sensor provides angular data, and I dont see within the manual a description of all the the functions contained within SparkFun_TMAG5273_Arduino_Library_Defs.h, SparkFun_TMAG5273_Arduino_Library_Defs.h is not commented enough that a begginer like myself can convert the TMAG data to simpleFOC hallsensor.h logic.

Currently INA240 & MPC6021 data is only described (as far as my abilities and travels have thus led me, I may have missed a doc) in the online hardware overview MKdoc with INA240 (U) on GPIO 35, INA240 (V) on GPIO 36, INA240 (W) on GPIO 39, MCP6021 on GPIO 32. I am wondering how to rectify these pin inputs with the simpleFOC InlineCurrentSense.h logic.

Thank you for any help you may have,
Waffle City, aiaaaa

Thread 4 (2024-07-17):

'mcpwm_isr_register' was not declared in this scope

fotherja, 2024-07-17:
Error trying to upload the standard firmware (IoT Motor Driver Example) that comes with IoT Brushless Motor Driver (from https://www.sparkfun.com/products/22132)

```
In file included from c:\Users\James\My Drive (fotherja@gmail.com)\5_Software\Arduino\Arduino\libraries\Simple_FOC\src\current_sense\hardware_specific\esp32\esp32_mcu.cpp:3:
c:\users\james\my drive (fotherja@gmail.com)\5_software\arduino\arduino\libraries\simple_foc\src\drivers\hardware_specific\esp32\esp32_driver_mcpwm.h:11:62: note: '#pragma message: SimpleFOC: compiling for ESP32 MCPWM driver'
   11 | #pragma message("SimpleFOC: compiling for ESP32 MCPWM driver")
      |                                                              ^
c:\Users\James\My Drive (fotherja@gmail.com)\5_Software\Arduino\Arduino\libraries\Simple_FOC\src\current_sense\hardware_specific\esp32\esp32_mcu.cpp: In function 'void _driverSyncLowSide(void*, void*)':
c:\Users\James\My Drive (fotherja@gmail.com)\5_Software\Arduino\Arduino\libraries\Simple_FOC\src\current_sense\hardware_specific\esp32\esp32_mcu.cpp:119:5: error: 'mcpwm_isr_register' was not declared in this scope
  119 |     mcpwm_isr_register(mcpwm_unit, mcpwm0_isr_handler, NULL, ESP_INTR_FLAG_IRAM, NULL);  //Set ISR Handler
      |     ^~~~~~~~~~~~~~~~~~
c:\Users\James\My Drive (fotherja@gmail.com)\5_Software\Arduino\Arduino\libraries\Simple_FOC\src\current_sense\hardware_specific\esp32\esp32_mcu.cpp:121:5: error: 'mcpwm_isr_register' was not declared in this scope
  121 |     mcpwm_isr_register(mcpwm_unit, mcpwm1_isr_handler, NULL, ESP_INTR_FLAG_IRAM, NULL);  //Set ISR Handler
      |     ^~~~~~~~~~~~~~~~~~

exit status 1

Compilation error: exit status 1
```

### Your workbench
* Arduino IDE 2.2.1
* Simple FOC 2.3.3 installed
* esp32 3.0.2 installed

I have set the board on the arduino IDE to ESP32 Thing Plus C as suggested in the Hookup guide by Sparkfun (https://docs.sparkfun.com/SparkFun_IoT_Brushless_Motor_Driver/software_overview/)

### Steps to reproduce
Simply having the above installed and trying to verify/upload the code

fotherja, 2024-07-22:
Just to add - I have set the board on the arduino IDE to ESP32 Thing Plus C as suggested in the Hookup guide by Sparkfun (https://docs.sparkfun.com/SparkFun_IoT_Brushless_Motor_Driver/software_overview/)

edspark, 2024-07-23:
Hello,

Luckily I was able to both reproduce and fix the issue that you were seeing. Simply update your Simple FOC library to the latest: 2.3.4, more details follow. In your output, it's clear that it's an issue with the "Simple FOC" library. When I installed version 2.3.3 (thanks for listing your version there) I was able to see the problem:

Shown below:
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

Checking the Simple [FOC 2.3.4 release](https://github.com/simplefoc/Arduino-FOC/releases/tag/v2.3.4), I see that they mention new support for the `MCPWM` driver. Which is why when I use 2.3.4, I no longer see the error:

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

I know the images aren't great, but I hope that helps.

Thanks!

fotherja, 2024-07-23:
Brilliant! Thank you very much for getting back to me. What convenient timing with the FOC update!

Closed 2024-07-23.

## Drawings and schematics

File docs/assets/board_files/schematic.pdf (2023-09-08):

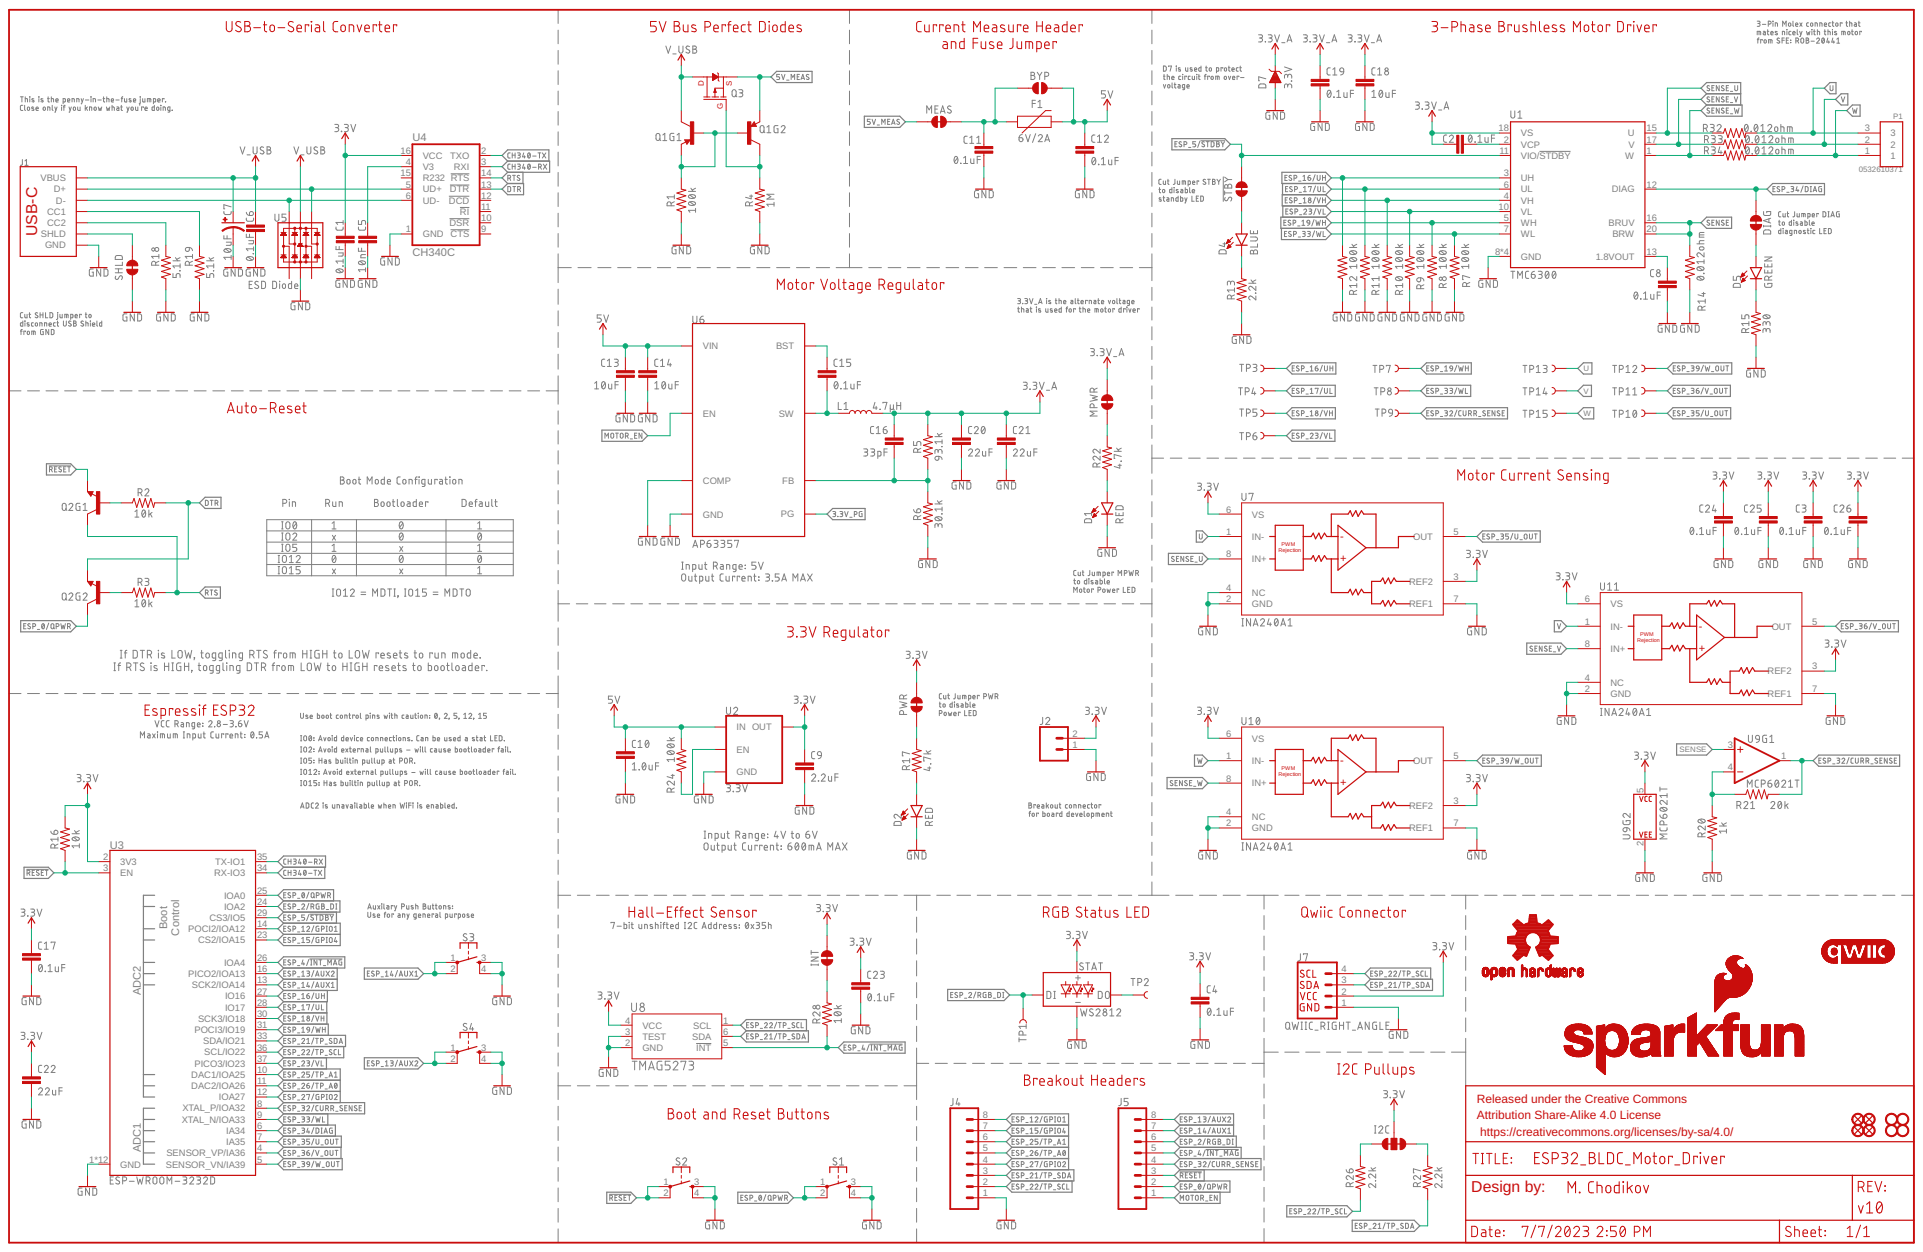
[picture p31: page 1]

ADC1 ADC2 Boot Control CH340C 0532610371 WH 5 W 1 GND 8*4 U 15 BRW 20 1.8VOUT 13 VIO/STDBY 11 VCP 2 UH 3 VH 4 DIAG 12 VS 18 UL 6 WL 7 BRUV 16 V 17 VL 10 GND VBUS CC1 D+D- CC2 SHLD 3V3 2 EN 3 SENSOR_VP/IA36 4 SENSOR_VN/IA39 5 IA34 6 IA35 7 XTAL_P/IOA32 8 XTAL_N/IOA33 9 DAC1/IOA25 10 DAC2/IOA26 11 IOA27 12 SCK2/IOA14 13 POCI2/IOA12 14 PICO2/IOA13 16 PICO3/IO23 37 SCL/IO22 36 TX-IO1 35 RX-IO3 34 SDA/IO21 33 POCI3/IO19 31 SCK3/IO18 30 CS3/IO5 29 IO17 28 IO16 27 IOA4 26 IOA0 25 IOA2 24 CS2/IOA15 23 GND 1*12U3 12345678 12345678 CTS 9 DCD 12 DSR 10 DTR 13 RI 11 RTS 14 GND 1 R232 15 RXI 3 TXO 2 UD+ 5 UD- 6 V3 4 VCC 16U4 1234 SCL 1 GND 2 TEST 3 VCC 4 INT 5 SDA 6 1 3 2 4 1 3 2 4 1 3 2 4 1 3 2 4 INGNDOUT EN 1 1 2 2 3 3 P1 VIN ENCOMP GND PGFB SWBST IN- 1 IN+ 8 REF1 7 REF2 3 NC 4 VS 6 GND 2 OUT 5 IN- 1 IN+ 8 REF1 7 REF2 3 NC 4 VS 6 GND 2 OUT 5 IN- 1 IN+ 8 REF1 7 REF2 3 NC 4 VS 6 GND 2 OUT 5 12 34 1 5 2 WVU SENSE Released under the Creative Commons Attribution Share-Alike 4.0 License https://creativecommons.org/licenses/by-sa/4.0/ Design by: USB-C DS G +- PWM Rejection +- PWM Rejection +- PWM Rejection

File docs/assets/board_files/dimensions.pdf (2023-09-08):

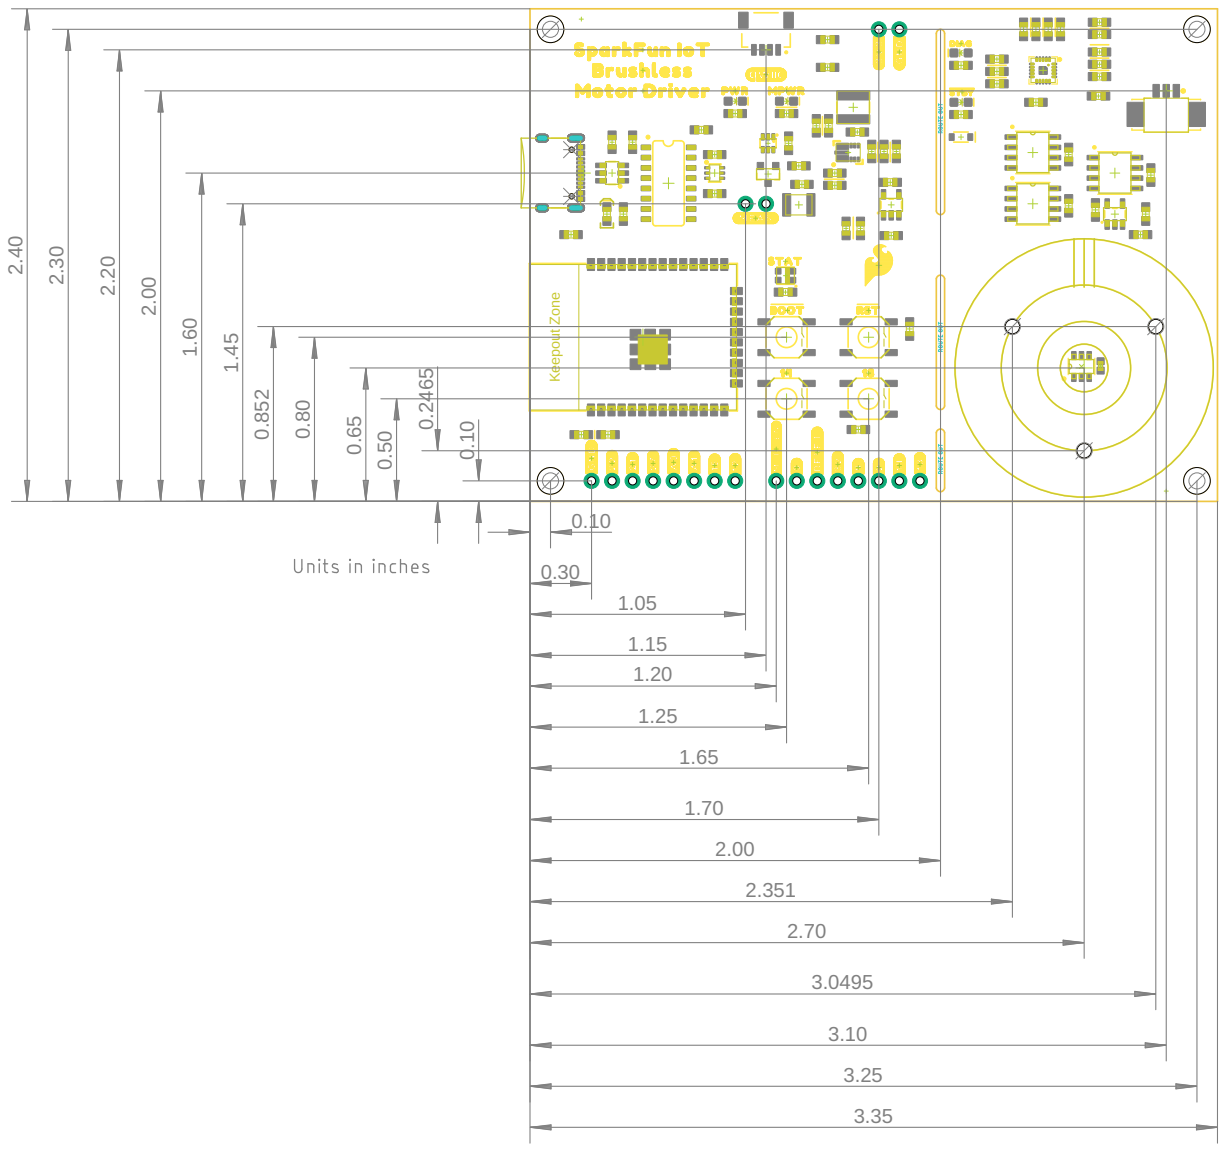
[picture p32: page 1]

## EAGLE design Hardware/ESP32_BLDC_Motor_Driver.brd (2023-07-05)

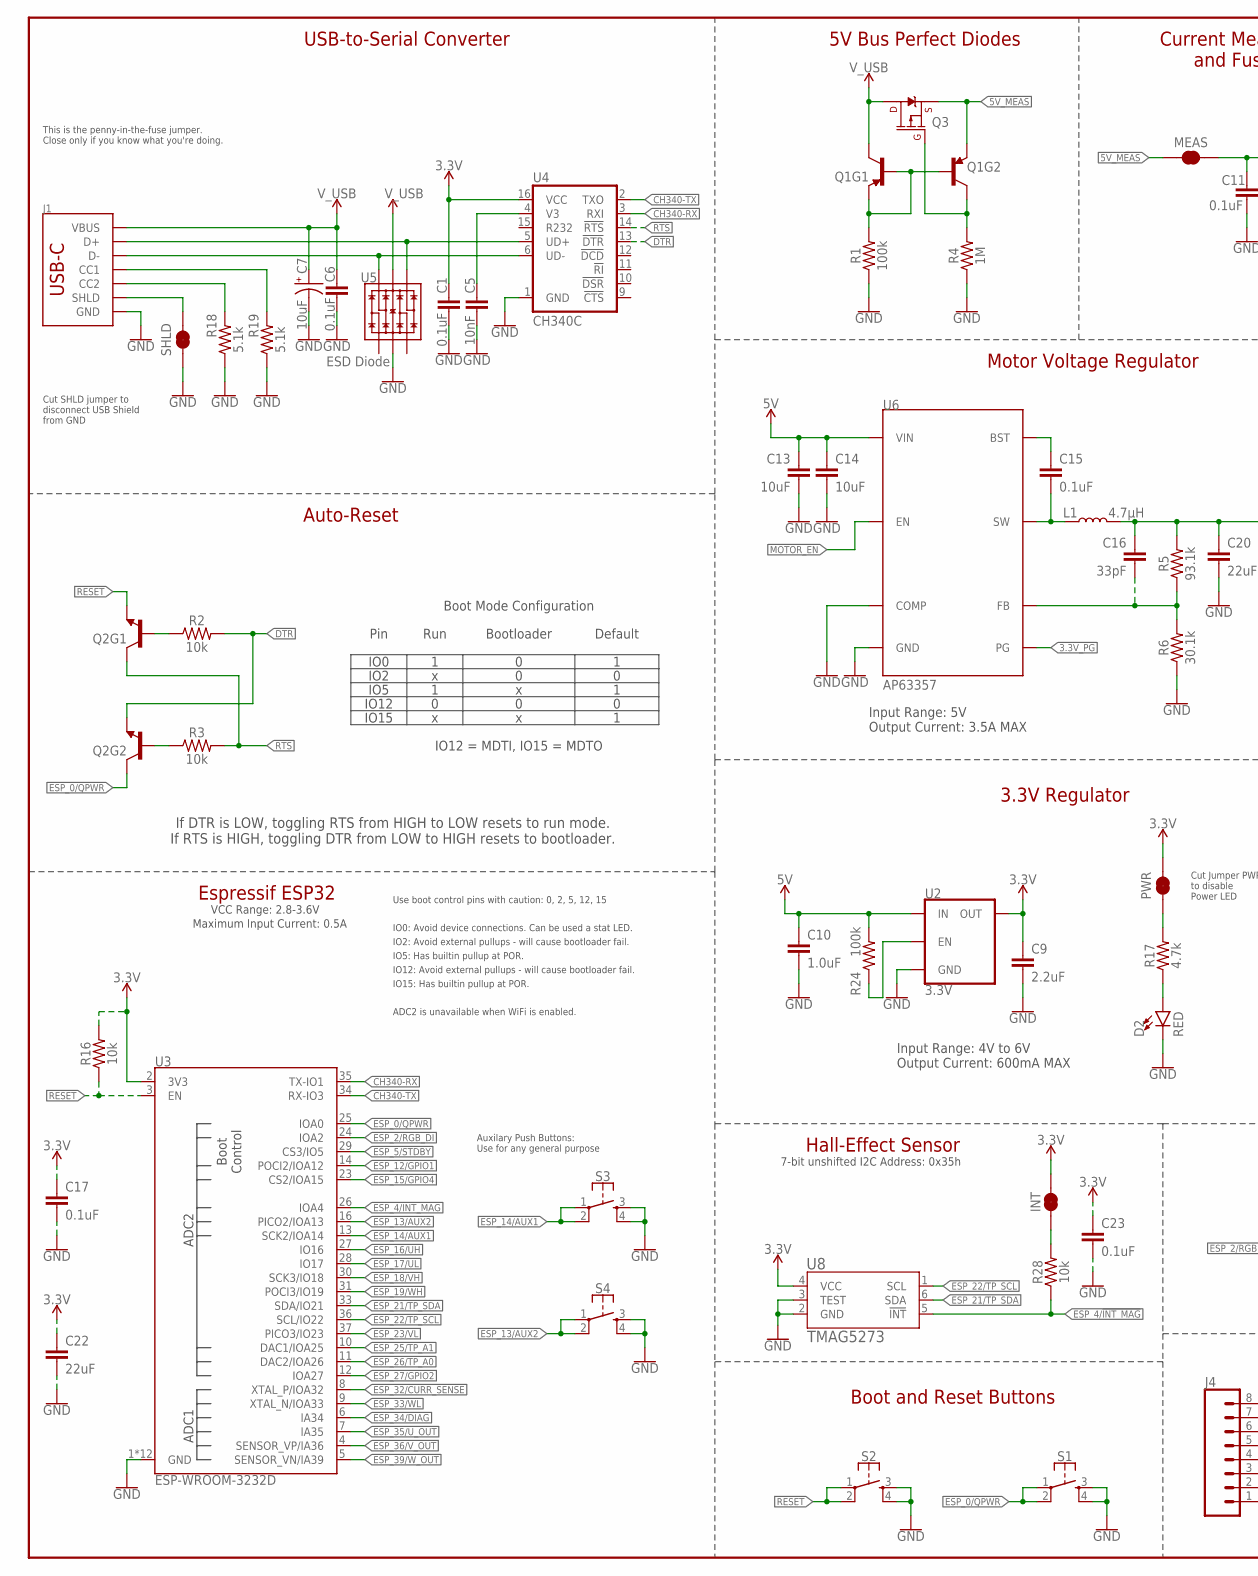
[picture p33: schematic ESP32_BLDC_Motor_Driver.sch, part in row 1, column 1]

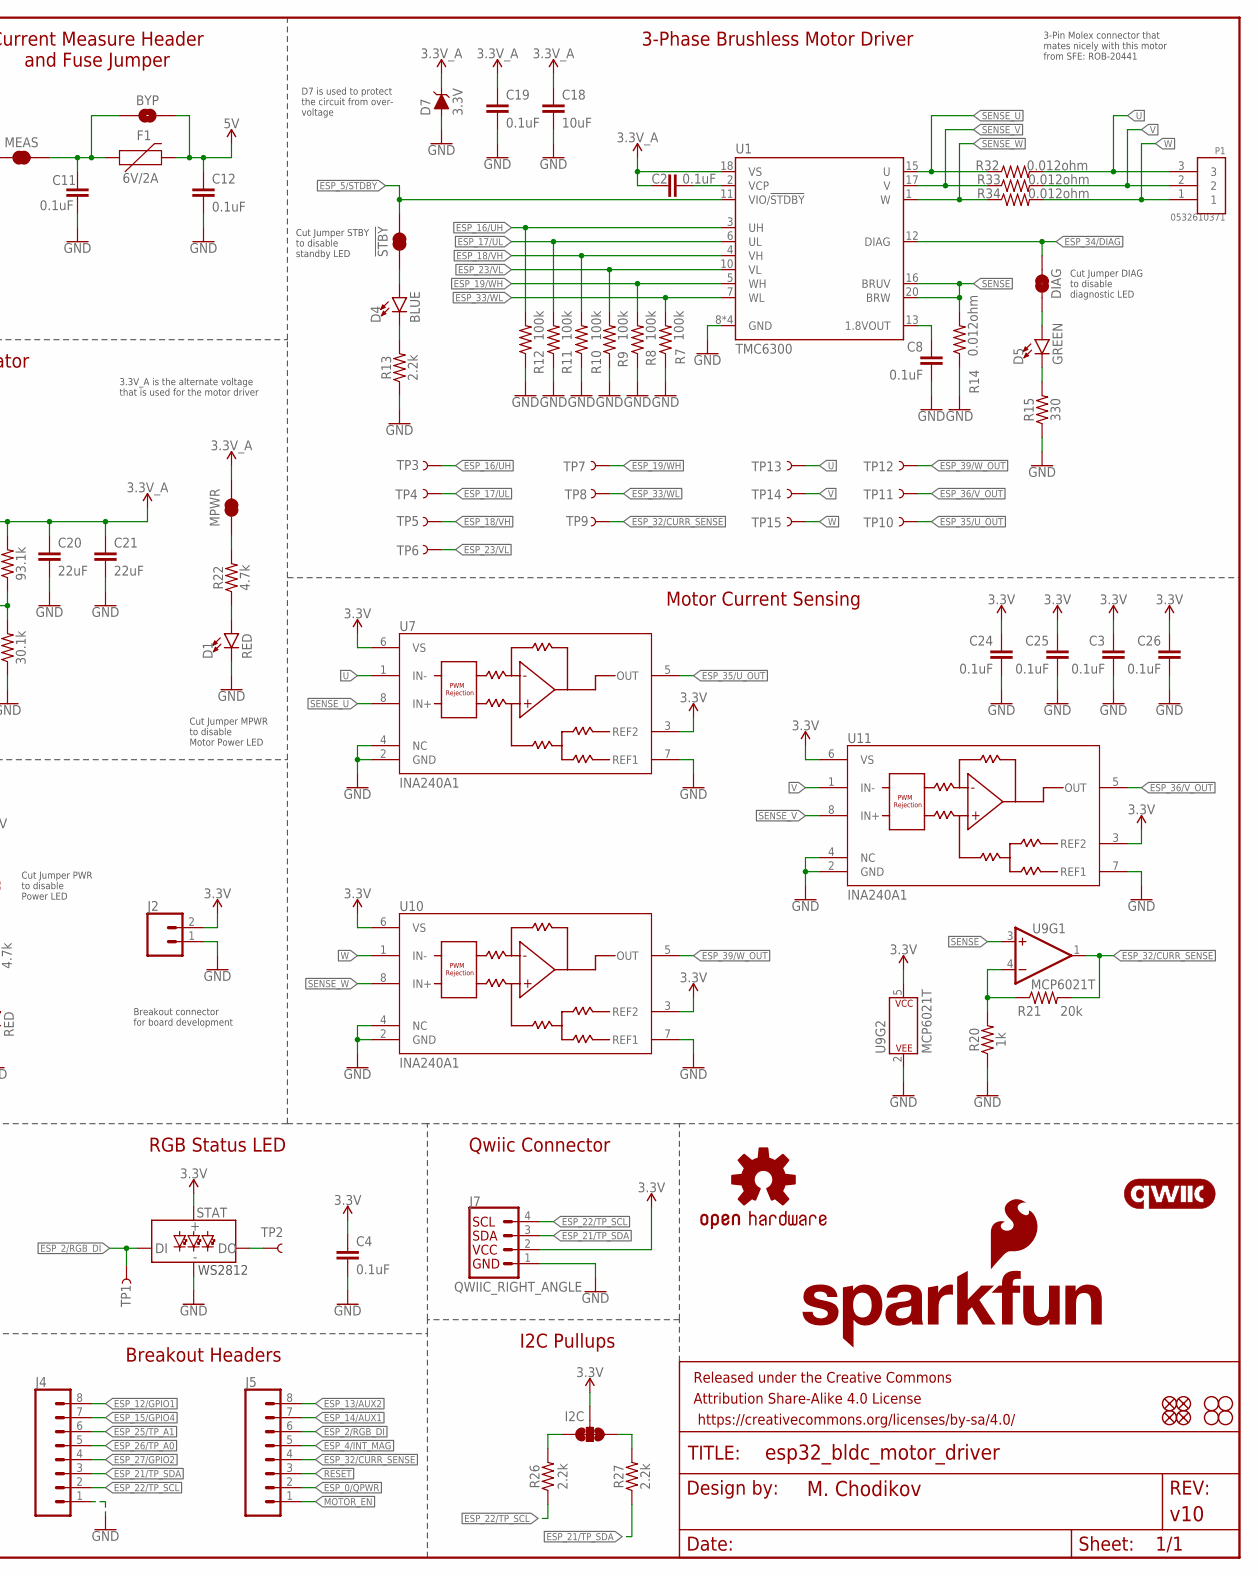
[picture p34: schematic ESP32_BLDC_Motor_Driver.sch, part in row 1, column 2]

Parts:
!STBY: JUMPER-SMT_2_NC_TRACE_SILK; SMT-JUMPER_2_NC_TRACE_SILK
BYP: JUMPER-SMT_2_NO_SILK; SMT-JUMPER_2_NO_SILK
C1, C2, C3, C4, C6, C8, C11, C12, C15, C17, C19, C24, C25, C26: 0.1uF; 0603
C5: 10nF; 0603
C7: 10uF; 0603-POLAR
C9: 2.2uF; 0603
C10: 1.0uF; 0603
C13, C14, C18: 10uF; 0603
C16: 33pF; 0603
C20, C21, C22: 22uF; 0603
C23: 0.1uF; 0402
D1, D2: RED; LED-0603
D4: BLUE; LED-0603
D5: GREEN; LED-0603
D7: 3.3V; SOD-323
DIAG: JUMPER-SMT_2_NC_TRACE_SILK; SMT-JUMPER_2_NC_TRACE_SILK
F1: 6V/2A; 1210
FD1, FD2, FD3, FD4: FIDUCIALUFIDUCIAL; FIDUCIAL-MICRO
FRAME1: FRAME-LEDGER; CREATIVE_COMMONS
H1, H2, H3, H4: STAND-OFF
I2C: JUMPER-SMT_3_2-NC_TRACE_SILK; SMT-JUMPER_3_2-NC_TRACE_SILK
INT: JUMPER-SMT_2_NC_TRACE_SILK; SMT-JUMPER_2_NC_TRACE_SILK
J1: USB-C Connector; USB-C-16P_4LAYER-PADS
J2: CONN_021X02_NO_SILK; 1X02_NO_SILK
J4: Breadboard Connector; 1X08_NO_SILK
J5: Breadboard Headers; 1X08_NO_SILK
J7: QWIIC_RIGHT_ANGLE; JST04_1MM_RA
L1: 4.7μH; INDUCTOR_4X4MM
LOGO1: SFE_LOGO_NAMEBLANK; BLANK
LOGO2: OSHW-LOGOM; OSHW-LOGO-M
LOGO3: SFE_LOGO_FLAME.2_INCH; SFE_LOGO_FLAME_.2
LOGO4: QWIIC_LOGO_5MM; QWIIC_5MM
MEAS: JUMPER-COMBO_2_NC_TRACE; COMBO-JUMPER_2_NC_TRACE
MPWR: JUMPER-SMT_2_NC_TRACE_SILK; SMT-JUMPER_2_NC_TRACE_SILK
P1: 0532610371; MOLEX_0532610371
PWR: JUMPER-SMT_2_NC_TRACE_SILK; SMT-JUMPER_2_NC_TRACE_SILK
Q1: TRANS_PNP_DUALSOT-363; SOT363_PHILIPS
Q2: NPN Transistors; SC70-6
Q3: 20V/4.2A/52mΩ/1.4W; SOT23-3
R1, R7, R8, R9, R10, R11, R12, R24: 100k; 0603
R2, R3, R16, R28: 10k; 0603
R4: 1M; 0603
R5: 93.1k; 0603
R6: 30.1k; 0603
R13, R26, R27: 2.2k; 0603
R14, R32, R33, R34: 0.012ohm; 0603
R15: 330; 0603
R17, R22: 4.7k; 0603
R18, R19: 5.1k; 0603
R20: 1k; 0603
R21: 20k; 0603
S1, S2, S3, S4: MOMENTARY-SWITCH-SPST-2-SMD-5.2MM-TALL; TACTILE_SWITCH_SMD_5.2MM
SHLD: JUMPER-SMT_2_NC_TRACE_SILK; SMT-JUMPER_2_NC_TRACE_SILK
STAT: WS2812_2020; WS2812-2020
TP1, TP2, TP3, TP4, TP5, TP6, TP7, TP8, TP9, TP10, TP11, TP12, TP13, TP14, TP15: TEST-POINT3X4; PAD.03X.04
U1: TMC6300; QFN-20
U2: 3.3V; SOT23-5
U3: ESP-WROOM-3232D; ESP-WROOM-32D
U4: CH340C; SO016
U5: ESD Diode; SOT-23-6
U6: AP63357; V-DFN3020-13
U7, U10, U11: INA240A1; D8_TEX
U8: TMAG5273; SOT23-6_DBV_TEX
U9: MCP6021T; SOT23-5

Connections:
1.8_VOUT: C8.1, U1.13 (1.8VOUT)
3.3V: C1.1, C3.1, C4.1, C9.1, C17.1, C22.1, C23.1, C24.1, C25.1, C26.1, I2C.2, INT.2, J2.2, J7.2, PWR.2, R16.2, STAT.VCC, U2.5 (OUT), U3.2 (3V3), U4.16 (VCC), U7.3 (REF2), U7.6 (VS), U8.4 (VCC), U9.5 (P$V+), U10.3 (REF2), U10.6 (VS), U11.3 (REF2), U11.6 (VS)
3.3V_A: C2.1, C16.2, C18.1, C19.1, C20.1, C21.1, D7.C, L1.P$2 (2), MPWR.2, R5.2, U1.18 (VS)
3.3V_PG: U6.P$5 (PG)
5V: BYP.2, C10.1, C12.1, C13.1, C14.1, F1.2, R24.2, U2.1 (IN), U6.P$1 (VIN)
5V_MEAS: MEAS.1, MEAS.3 (1), Q1.4 (E), Q3.2 (S)
!RESET: J5.3, Q2.4 (E), R16.1, S2.1, S2.2, U3.3 (EN)
BST: C15.1, U6.P$6 (BST)
CH340-RX: U3.35 (TX-IO1), U4.3 (RXI)
CH340-TX: U3.34 (RX-IO3), U4.2 (TXO)
D: D5.A, DIAG.1
D+: J1.A6 (D+), J1.B6 (D+), U4.5 (UD+), U5.4 (IO3)
D-: J1.A7 (D-), J1.B7 (D-), U4.6 (UD-), U5.6 (IO4)
DTR: Q2.1 (E), R2.2, U4.13 (!DTR)
ESP_0/QPWR: J5.2, Q2.6 (C), S1.1, S1.2, U3.25 (IOA0)
ESP_2/RGB_DI: J5.6, STAT.DI, TP1.1, U3.24 (IOA2)
ESP_4/!INT_MAG: J5.5, R28.1, U3.26 (IOA4), U8.5 (!INT)
ESP_5/!STDBY: !STBY.2, U1.11 (VIO/!STDBY!), U3.29 (CS3/IO5)
ESP_12/GPIO1: J4.8, U3.14 (POCI2/IOA12)
ESP_13/AUX2: J5.8, S4.1, S4.2, U3.16 (PICO2/IOA13)
ESP_14/AUX1: J5.7, S3.1, S3.2, U3.13 (SCK2/IOA14)
ESP_15/GPIO4: J4.7, U3.23 (CS2/IOA15)
ESP_16/UH: R12.2, TP3.1, U1.3 (UH), U3.27 (IO16)
ESP_17/UL: R11.2, TP4.1, U1.6 (UL), U3.28 (IO17)
ESP_18/VH: R10.2, TP5.1, U1.4 (VH), U3.30 (SCK3/IO18)
ESP_19/WH: R8.2, TP7.1, U1.5 (WH), U3.31 (POCI3/IO19)
ESP_21/TP_SDA: J4.3, J7.3, R27.1, U3.33 (SDA/IO21), U8.6 (SDA)
ESP_22/TP_SCL: J4.2, J7.4, R26.1, U3.36 (SCL/IO22), U8.1 (SCL)
ESP_23/VL: R9.2, TP6.1, U1.10 (VL), U3.37 (PICO3/IO23)
ESP_25/TP_A1: J4.6, U3.10 (DAC1/IOA25)
ESP_26/TP_A0: J4.5, U3.11 (DAC2/IOA26)
ESP_27/GPIO2: J4.4, U3.12 (IOA27)
ESP_32/CURR_SENSE: J5.4, R21.2, TP9.1, U3.8 (XTAL_P/IOA32), U9.1 (OUT)
ESP_33/WL: R7.2, TP8.1, U1.7 (WL), U3.9 (XTAL_N/IOA33)
ESP_34/DIAG: DIAG.2, U1.12 (DIAG), U3.6 (IA34)
ESP_35/U_OUT: TP10.1, U3.7 (IA35), U7.5 (OUT)
ESP_36/V_OUT: TP11.1, U3.4 (SENSOR_VP/IA36), U11.5 (OUT)
ESP_39/W_OUT: TP12.1, U3.5 (SENSOR_VN/IA39), U10.5 (OUT)
FB: C16.1, R5.1, R6.2, U6.P$3 (FB)
GND: C1.2, C3.2, C4.2, C5.2, C6.2, C7.-, C8.2, C9.2, C10.2, C11.2, C12.2, C13.2, C14.2, C17.2, C18.2, C19.2, C20.2, C21.2, C22.2, C23.2, C24.2, C25.2, C26.2, D1.C, D2.C, D7.A, J1.GND, J1.GND2 (GND), J2.1, J4.1, J7.1, R1.1, R4.1, R6.1, R7.1, R8.1, R9.1, R10.1, R11.1, R12.1, R13.1, R14.1, R15.1, R18.1, R19.1, R20.1, S1.3, S1.4, S2.3, S2.4, S3.3, S3.4, S4.3, S4.4, SHLD.1, STAT.GND, U1.8 (GND), U1.9 (GND), U1.14 (GND), U1.PAD (GND), U2.2 (GND), U3.1 (GND), U3.15 (GND), U3.38 (GND), U3.GND, U3.GNDT1 (GND), U3.GNDT2 (GND), U3.GNDT3 (GND), U3.GNDT4 (GND), U3.GNDT5 (GND), U3.GNDT6 (GND), U3.GNDT7 (GND), U3.GNDT8 (GND), U4.1 (GND), U5.2 (VSS), U6.P$4 (COMP), U6.P$8 (GND), U7.2 (GND), U7.4 (NC), U7.7 (REF1), U8.2 (GND), U8.3 (TEST), U9.2 (P$V-), U10.2 (GND), U10.4 (NC), U10.7 (REF1), U11.2 (GND), U11.4 (NC), U11.7 (REF1)
MOTOR_EN: J5.1, U6.P$2 (EN)
unnamed: J1.A5 (CC1), R19.2
unnamed: C5.1, U4.4 (V3)
unnamed: J1.B5 (CC2), R18.2
unnamed: C2.2, U1.2 (VCP)
unnamed: R24.1, U2.3 (EN)
unnamed: Q2.5 (B), R2.1
unnamed: Q2.2 (B), R3.1
unnamed: D2.A, R17.1
unnamed: INT.1, R28.2
unnamed: I2C.3, R26.2
unnamed: I2C.1, R27.2
unnamed: R20.2, R21.1, U9.4 (-IN)
unnamed: PWR.1, R17.2
unnamed: BYP.1, C11.1, F1.1, MEAS.2, MEAS.4 (2)
unnamed: Q1.3 (C), Q3.1 (G), R4.2
unnamed: Q1.1 (E), Q1.2 (B), Q1.5 (B), R1.2
unnamed: D1.A, R22.1
unnamed: MPWR.1, R22.2
unnamed: D4.C, R13.2
unnamed: D5.C, R15.2
RTS: Q2.3 (C), R3.2, U4.14 (!RTS)
S: !STBY.1, D4.A
SENSE: R14.2, U1.16 (BRUV), U1.20 (BRW), U9.3 (+IN)
SENSE_U: R32.1, U1.15 (U), U7.8 (IN+)
SENSE_V: R33.1, U1.17 (V), U11.8 (IN+)
SENSE_W: R34.1, U1.1 (W), U10.8 (IN+)
SHLD: J1.SHLD1 (SHLD), J1.SHLD2 (SHLD), J1.SHLD3 (SHLD), J1.SHLD4 (SHLD), SHLD.2
SW: C15.2, L1.P$1 (1), U6.P$7 (SW), U6.P$9 (SW)
TP2: STAT.DO, TP2.1
U: P1.3, R32.2, TP13.1, U7.1 (IN-)
V: P1.2, R33.2, TP14.1, U11.1 (IN-)
V_USB: C6.1, C7.+, J1.VBUS1 (VBUS), J1.VBUS2 (VBUS), Q1.6 (C), Q3.3 (D), U5.5 (VCC)
W: P1.1, R34.2, TP15.1, U10.1 (IN-)

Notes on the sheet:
Espressif ESP32
VCC Range: 2.8-3.6V
3-Phase Brushless Motor Driver
USB-to-Serial Converter
Cut Jumper DIAG to disable diagnostic LED
Cut Jumper STBY to disable standby LED
Breakout Headers
Auto-Reset
Boot and Reset Buttons
If DTR is LOW, toggling RTS from HIGH to LOW resets to run mode. If RTS is HIGH, toggling DTR from LOW to HIGH resets to bootloader.
3.3V Regulator
3-Pin Molex connector that mates nicely with this motor from SFE: ROB-20441
Cut SHLD jumper to disconnect USB Shield from GND
This is the penny-in-the-fuse jumper. Close only if you know what you're doing.
Pin
IO0
IO2
IO12
IO15
IO5
Run
Bootloader
Default
IO12 = MDTI, IO15 = MDTO
Boot Mode Configuration
RGB Status LED
IO0: Avoid device connections. Can be used a stat LED.
ADC2 is unavailable when WiFi is enabled.
IO12: Avoid external pullups - will cause bootloader fail.
Use boot control pins with caution: 0, 2, 5, 12, 15
IO2: Avoid external pullups - will cause bootloader fail.
IO15: Has builtin pullup at POR.
IO5: Has builtin pullup at POR.
Qwiic Connector
Auxilary Push Buttons: Use for any general purpose
WS2812
Hall-Effect Sensor
Maximum Input Current: 0.5A
7-bit unshifted I2C Address: 0x35h
D7 is used to protect the circuit from over- voltage

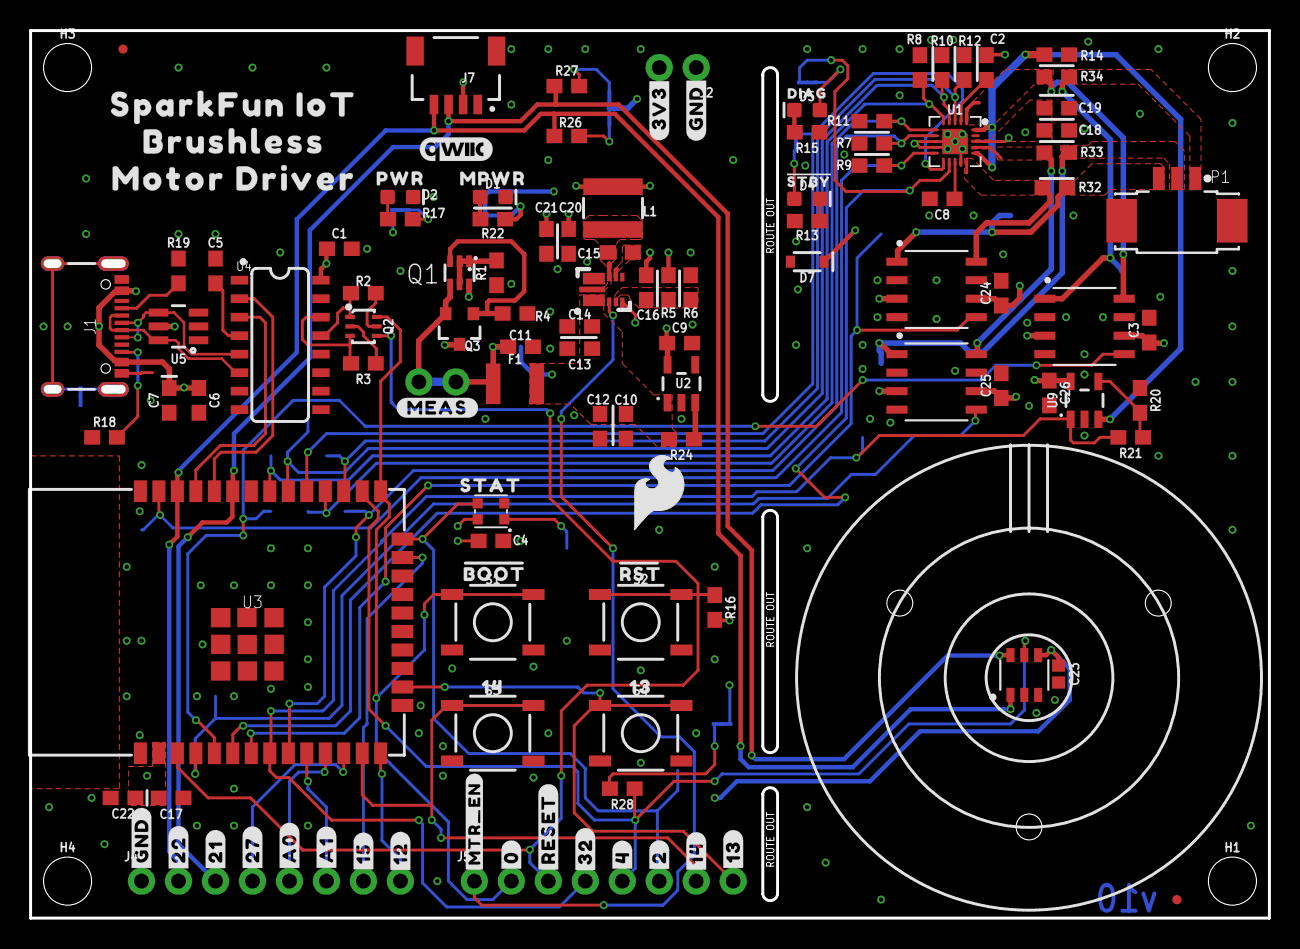
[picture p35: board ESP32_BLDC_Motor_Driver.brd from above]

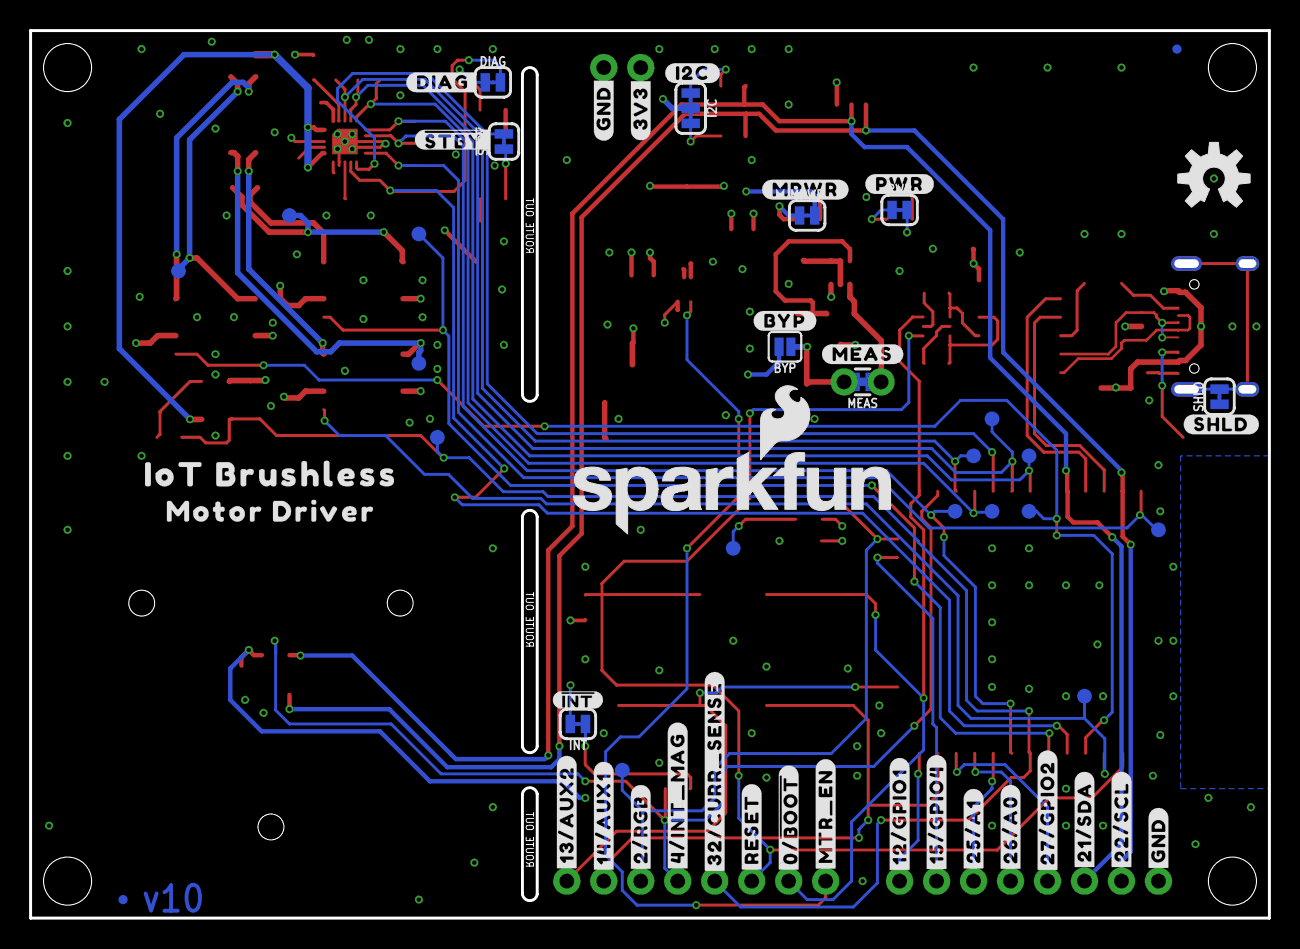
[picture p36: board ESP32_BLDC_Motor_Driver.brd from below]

Board: 4 copper layers, 85.1 x 61.0 mm, 187 parts (58 on the bottom side), 73 nets.

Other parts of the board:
U$1: ORDERING_INSTRUCTIONS
U$2: OT-EM3215
U$3: 1436
U$4: STAT1630063003522
U$5: RST1630063003525
U$6: #14#AUX1#36
U$7: #12#31
U$8: #DIAG#15
U$9: #14#36
U$10: ##STBY##16
U$11: BOOT21630063003532
U$12: PWR21630063003533
U$13: #MTR_EN#131458
U$14, U$15: #GND#32
U$16, U$58: #3V3#18
U$17: #4#INT_MAG#21630063003534
U$18: #22#33
U$19: #21#33
U$20: #MPWR#131468
U$21: #27#33
U$22: #15#33
U$23: #I2C#630063003467
U$24: #SHLD#630063003467
U$25: ##INT#630063003473
U$26: #32#CURR_SENSE#10
U$27: #PWR#33
U$28, U$60: #GND#17
U$29, U$30: #RESET#34
U$31: #0#33
U$32: #0##BOOT##0
U$33: #32#33
U$34: #4#33
U$35: #12#GPIO1#4
U$36: #2#33
U$37: #15#GPIO4#13
U$38: #13#36
U$39: 131437
U$40: #26#A0#30
U$41: #25#A1#30
U$42: #A1#30
U$43: #BYP#131439
U$44: SPARKFUN_IOT131442
U$45: SFE_LOGO_NAME_FLAME_.2
U$46: BRUSHLESS131445
U$47: MOTOR_DRIVER131446
U$48, U$50: #MEAS#131453
U$49: MPWR131449
U$51: #MTR_EN#131460
U$52: #13#AUX2#14
U$53: #STBY#131470
U$54: #27#GPIO2#27
U$55: IOT_BRUSHLESS131454
U$56: #21#SDA#29
U$57: DIAG131469
U$59: #2#RGB#18
U$62: MOTOR_DRIVER630063003515
U$63: #22#SCL#30
U$64: #A0#30

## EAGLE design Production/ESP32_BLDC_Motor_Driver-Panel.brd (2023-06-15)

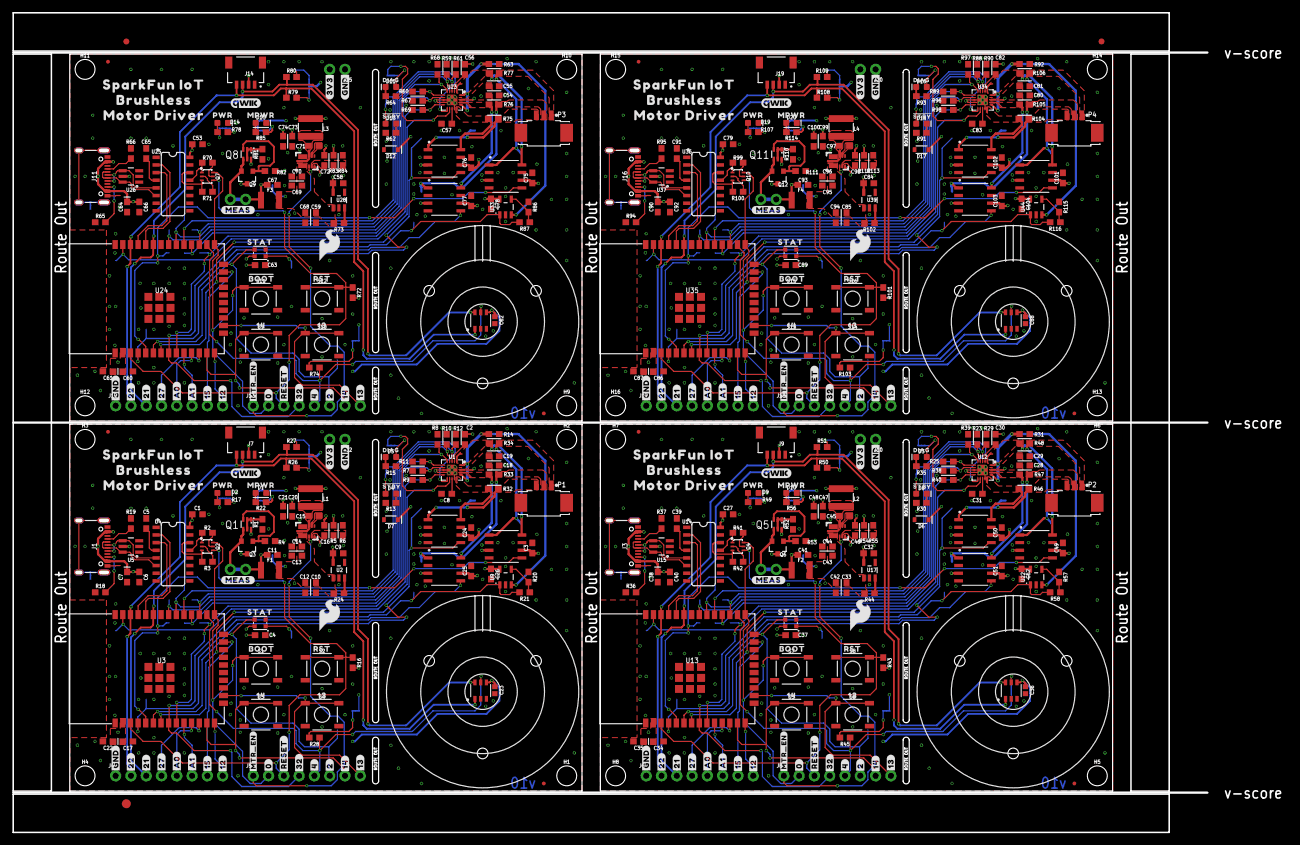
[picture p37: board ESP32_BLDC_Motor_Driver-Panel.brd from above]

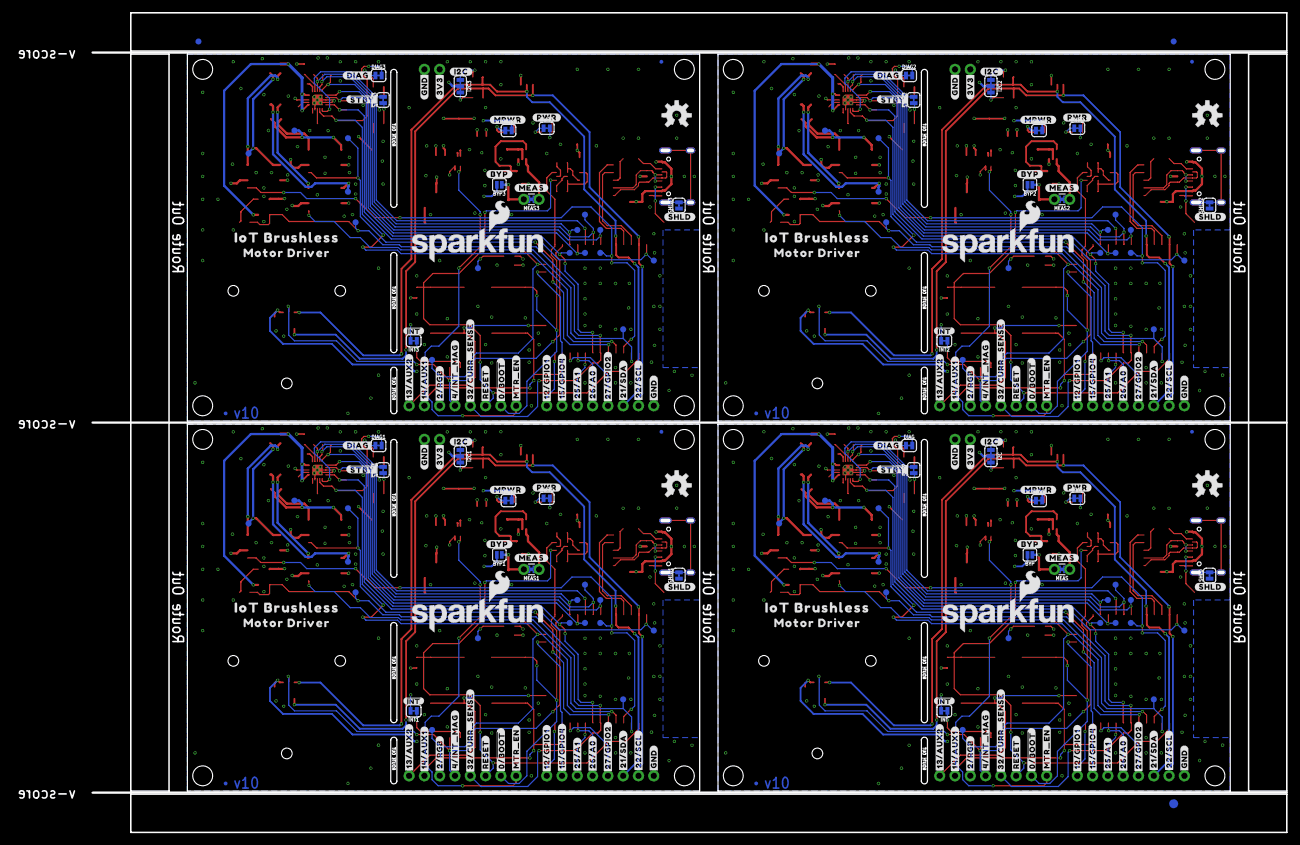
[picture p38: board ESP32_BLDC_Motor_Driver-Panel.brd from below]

Board: 4 copper layers, 198.4 x 136.1 mm, 750 parts (235 on the bottom side), 292 nets.

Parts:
!STBY, !STBY1, !STBY2, !STBY3: JUMPER-SMT_2_NC_TRACE_SILK; SMT-JUMPER_2_NC_TRACE_SILK
BYP, BYP1, BYP2, BYP3: JUMPER-SMT_2_NO_SILK; SMT-JUMPER_2_NO_SILK
C1, C2, C3, C4, C6, C8, C11, C12, C15, C17, C19, C24, C25, C26, C27, C29, C30, C31, C34, C37, C40, C41, C42, C45, C49, C50, C51, C52, C53, C55, C56, C57, C60, C63, C66, C67, C68, C71, C75, C76, C77, C78, C79, C81, C82, C83, C86, C89, C92, C93, C94, C97, C101, C102, C103, C104: 0.1uF; 0603
C5, C39, C65, C91: 10nF; 0603
C7, C38, C64, C90: 10uF; 0603-POLAR
C9, C32, C58, C84: 2.2uF; 0603
C10, C33, C59, C85: 1.0uF; 0603
C13, C14, C18, C28, C43, C44, C54, C69, C70, C80, C95, C96: 10uF; 0603
C16, C46, C72, C98: 33pF; 0603
C20, C21, C22, C35, C47, C48, C61, C73, C74, C87, C99, C100: 22uF; 0603
C23, C36, C62, C88: 0.1uF; 0402
D1, D2, D9, D10, D14, D15, D19, D20: RED; LED-0603
D3, D5, D11, D16: GREEN; LED-0603
D4, D8, D13, D18: BLUE; LED-0603
D6, D7, D12, D17: 3.3V; SOD-323
DIAG, DIAG1, DIAG2, DIAG3: JUMPER-SMT_2_NC_TRACE_SILK; SMT-JUMPER_2_NC_TRACE_SILK
E$1, E$2, E$3, E$4: FIDUCIAL-1X2
E$5, E$6: FIDUCIAL-1.5X3
F1, F2, F3, F4: 6V/2A; 1210
FD1, FD2, FD3, FD4, FD5, FD6, FD7, FD8, FD9, FD10, FD11, FD12, FD13, FD14, FD15, FD16: FIDUCIALUFIDUCIAL; FIDUCIAL-MICRO
H1, H2, H3, H4, H5, H6, H7, H8, H9, H10, H11, H12, H13, H14, H15, H16: STAND-OFF
I2C, I2C1, I2C2, I2C3: JUMPER-SMT_3_2-NC_TRACE_SILK; SMT-JUMPER_3_2-NC_TRACE_SILK
INT, INT1, INT2, INT3: JUMPER-SMT_2_NC_TRACE_SILK; SMT-JUMPER_2_NC_TRACE_SILK
J1, J3, J11, J16: USB-C Connector; USB-C-16P_4LAYER-PADS
J2, J10, J15, J20: 1X02_NO_SILK
J4, J6, J12, J17: Breadboard Connector; 1X08_NO_SILK
J5, J8, J13, J18: Breadboard Headers; 1X08_NO_SILK
J7, J9, J14, J19: QWIIC_RIGHT_ANGLE; JST04_1MM_RA
L1, L2, L3, L4: 4.7μH; INDUCTOR_4X4MM
LOGO1, LOGO8, LOGO12, LOGO16: SFE_LOGO_NAMEBLANK; BLANK
LOGO2, LOGO5, LOGO9, LOGO13: OSHW-LOGOM; OSHW-LOGO-M
LOGO3, LOGO6, LOGO10, LOGO14: SFE_LOGO_FLAME.2_INCH; SFE_LOGO_FLAME_.2
LOGO4, LOGO7, LOGO11, LOGO15: QWIIC_LOGO_5MM; QWIIC_5MM
MEAS, MEAS1, MEAS2, MEAS3: JUMPER-COMBO_2_NC_TRACE; COMBO-JUMPER_2_NC_TRACE
MPWR, MPWR1, MPWR2, MPWR3: JUMPER-SMT_2_NC_TRACE_SILK; SMT-JUMPER_2_NC_TRACE_SILK
P1, P2, P3, P4: 0532610371; MOLEX_0532610371
PWR, PWR1, PWR2, PWR3: JUMPER-SMT_2_NC_TRACE_SILK; SMT-JUMPER_2_NC_TRACE_SILK
Q1, Q5, Q8, Q11: SOT363_PHILIPS
Q2, Q4, Q7, Q10: NPN Transistors; SC70-6
Q3, Q6, Q9, Q12: 20V/4.2A/52mΩ/1.4W; SOT23-3
R1, R7, R8, R9, R10, R11, R12, R23, R24, R25, R29, R38, R39, R40, R44, R52, R59, R60, R61, R67, R68, R69, R73, R81, R88, R89, R90, R96, R97, R98, R102, R110: 100k; 0603
R2, R3, R16, R28, R41, R42, R43, R45, R70, R71, R72, R74, R99, R100, R101, R103: 10k; 0603
R4, R53, R82, R111: 1M; 0603
R5, R54, R83, R112: 93.1k; 0603
R6, R55, R84, R113: 30.1k; 0603
R13, R26, R27, R30, R50, R51, R62, R79, R80, R91, R108, R109: 2.2k; 0603
R14, R31, R32, R33, R34, R46, R47, R48, R63, R75, R76, R77, R92, R104, R105, R106: 0.012ohm; 0603
R15, R35, R64, R93: 330; 0603
R17, R22, R49, R56, R78, R85, R107, R114: 4.7k; 0603
R18, R19, R36, R37, R65, R66, R94, R95: 5.1k; 0603
R20, R57, R86, R115: 1k; 0603
R21, R58, R87, R116: 20k; 0603
S1, S2, S3, S4, S5, S6, S7, S8, S9, S10, S11, S12, S13, S14, S15, S16: TACTILE_SWITCH_SMD_5.2MM
SHLD, SHLD1, SHLD2, SHLD3: JUMPER-SMT_2_NC_TRACE_SILK; SMT-JUMPER_2_NC_TRACE_SILK
STAT, STAT1, STAT2, STAT3: WS2812_2020; WS2812-2020
TP1, TP2, TP3, TP4, TP5, TP6, TP7, TP8, TP9, TP10, TP11, TP12, TP13, TP14, TP15, TP16, TP17, TP18, TP19, TP20, TP21, TP22, TP23, TP24, TP25, TP26, TP27, TP28, TP29, TP30, TP31, TP32, TP33, TP34, TP35, TP36, TP37, TP38, TP39, TP40, TP41, TP42, TP43, TP44, TP45, TP46, TP47, TP48, TP49, TP50, TP51, TP52, TP53, TP54, TP55, TP56, TP57, TP58, TP59, TP60: TEST-POINT3X4; PAD.03X.04
U1, U12, U23, U34: TMC6300; QFN-20
U2, U17, U28, U39: 3.3V; SOT23-5
U3, U13, U24, U35: ESP-WROOM-3232D; ESP-WROOM-32D
U4, U14, U25, U36: CH340C; SO016
U5, U15, U26, U37: ESD Diode; SOT-23-6
U6, U18, U29, U40: AP63357; V-DFN3020-13
U7, U10, U11, U19, U20, U21, U30, U31, U32, U41, U42, U43: INA240A1; D8_TEX
U8, U16, U27, U38: TMAG5273; SOT23-6_DBV_TEX
U9, U22, U33, U44: OPA344; SOT23-5
U$1, U$61, U$127, U$190: ORDERING_INSTRUCTIONS
U$2, U$70, U$133, U$196: OT-EM3215
U$3, U$103, U$166, U$229: 1436
U$4, U$71, U$134, U$197: STAT1630063003522
U$5, U$72, U$135, U$198: RST1630063003525
U$6, U$100, U$163, U$226: #14#AUX1#36
U$7, U$89, U$152, U$215: #12#31
U$8, U$119, U$182, U$245: #DIAG#15
U$9, U$101, U$164, U$227: #14#36
U$10, U$120, U$183, U$246: ##STBY##16
U$11, U$73, U$136, U$199: BOOT21630063003532
U$12, U$74, U$137, U$200: PWR21630063003533
U$13, U$113, U$176, U$239: #MTR_EN#131458
U$14, U$15, U$90, U$91, U$153, U$154, U$216, U$217: #GND#32
U$16, U$58, U$122, U$124, U$185, U$187, U$248, U$250: #3V3#18
U$17, U$75, U$138, U$201: #4#INT_MAG#21630063003534
U$18, U$92, U$155, U$218: #22#33
U$19, U$93, U$156, U$219: #21#33
U$20, U$115, U$178, U$241: #MPWR#131468
U$21, U$94, U$157, U$220: #27#33
U$22, U$95, U$158, U$221: #15#33
U$23, U$65, U$128, U$191: #I2C#630063003467
U$24, U$66, U$129, U$192: #SHLD#630063003467
U$25, U$67, U$130, U$193: ##INT#630063003473
U$26, U$76, U$139, U$202: #32#CURR_SENSE#10
U$27, U$77, U$140, U$203: #PWR#33
U$28, U$60, U$121, U$125, U$184, U$188, U$247, U$251: #GND#17
U$29, U$30, U$78, U$79, U$141, U$142, U$204, U$205: #RESET#34
U$31, U$96, U$159, U$222: #0#33
U$32, U$126, U$189, U$252: #0##BOOT##0
U$33, U$97, U$160, U$223: #32#33
U$34, U$98, U$161, U$224: #4#33
U$35, U$80, U$143, U$206: #12#GPIO1#4
U$36, U$99, U$162, U$225: #2#33
U$37, U$81, U$144, U$207: #15#GPIO4#13
U$38, U$102, U$165, U$228: #13#36
U$39, U$104, U$167, U$230: 131437
U$40, U$86, U$149, U$212: #26#A0#30
U$41, U$87, U$150, U$213: #25#A1#30
U$42, U$88, U$151, U$214: #A1#30
U$43, U$105, U$168, U$231: #BYP#131439
U$44, U$106, U$169, U$232: SPARKFUN_IOT131442
U$45, U$68, U$131, U$194: SFE_LOGO_NAME_FLAME_.2
U$46, U$107, U$170, U$233: BRUSHLESS131445
U$47, U$108, U$171, U$234: MOTOR_DRIVER131446
U$48, U$50, U$110, U$111, U$173, U$174, U$236, U$237: #MEAS#131453
U$49, U$109, U$172, U$235: MPWR131449
U$51, U$114, U$177, U$240: #MTR_EN#131460
U$52, U$118, U$181, U$244: #13#AUX2#14
U$53, U$117, U$180, U$243: #STBY#131470
U$54, U$82, U$145, U$208: #27#GPIO2#27
U$55, U$112, U$175, U$238: IOT_BRUSHLESS131454
U$56, U$83, U$146, U$209: #21#SDA#29
U$57, U$116, U$179, U$242: DIAG131469
U$59, U$123, U$186, U$249: #2#RGB#18
U$62, U$69, U$132, U$195: MOTOR_DRIVER630063003515
U$63, U$84, U$147, U$210: #22#SCL#30
U$64, U$85, U$148, U$211: #A0#30

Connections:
1.8_VOUT: C8.1, U1.13
1.8_VOUT1: C31.1, U12.13
1.8_VOUT2: C57.1, U23.13
1.8_VOUT3: C83.1, U34.13
3.3V: C1.1, C3.1, C4.1, C9.1, C17.1, C22.1, C23.1, C24.1, C25.1, C26.1, I2C.2, INT.2, J2.2, J7.2, PWR.2, R16.2, STAT.VCC, U2.5, U3.2, U4.16, U7.3, U7.6, U8.4, U9.5, U10.3, U10.6, U11.3, U11.6
3.3V1: C27.1, C32.1, C34.1, C35.1, C36.1, C37.1, C49.1, C50.1, C51.1, C52.1, I2C1.2, INT1.2, J9.2, J10.2, PWR1.2, R43.2, STAT1.VCC, U13.2, U14.16, U16.4, U17.5, U19.3, U19.6, U20.3, U20.6, U21.3, U21.6, U22.5
3.3V2: C53.1, C58.1, C60.1, C61.1, C62.1, C63.1, C75.1, C76.1, C77.1, C78.1, I2C2.2, INT2.2, J14.2, J15.2, PWR2.2, R72.2, STAT2.VCC, U24.2, U25.16, U27.4, U28.5, U30.3, U30.6, U31.3, U31.6, U32.3, U32.6, U33.5
3.3V3: C79.1, C84.1, C86.1, C87.1, C88.1, C89.1, C101.1, C102.1, C103.1, C104.1, I2C3.2, INT3.2, J19.2, J20.2, PWR3.2, R101.2, STAT3.VCC, U35.2, U36.16, U38.4, U39.5, U41.3, U41.6, U42.3, U42.6, U43.3, U43.6, U44.5
3.3V_A: C2.1, C16.2, C18.1, C19.1, C20.1, C21.1, D7.C, L1.P$2, MPWR.2, R5.2, U1.18
3.3V_A1: C28.1, C29.1, C30.1, C46.2, C47.1, C48.1, D6.C, L2.P$2, MPWR1.2, R54.2, U12.18
3.3V_A2: C54.1, C55.1, C56.1, C72.2, C73.1, C74.1, D12.C, L3.P$2, MPWR2.2, R83.2, U23.18
3.3V_A3: C80.1, C81.1, C82.1, C98.2, C99.1, C100.1, D17.C, L4.P$2, MPWR3.2, R112.2, U34.18
5V: BYP.2, C10.1, C12.1, C13.1, C14.1, F1.2, R24.2, U2.1, U6.P$1
5V1: BYP1.2, C33.1, C42.1, C43.1, C44.1, F2.2, R44.2, U17.1, U18.P$1
5V2: BYP2.2, C59.1, C68.1, C69.1, C70.1, F3.2, R73.2, U28.1, U29.P$1
5V3: BYP3.2, C85.1, C94.1, C95.1, C96.1, F4.2, R102.2, U39.1, U40.P$1
5V_MEAS: MEAS.1, MEAS.3, Q1.4, Q3.2
5V_MEAS1: MEAS1.1, MEAS1.3, Q5.4, Q6.2
5V_MEAS2: MEAS2.1, MEAS2.3, Q8.4, Q9.2
5V_MEAS3: MEAS3.1, MEAS3.3, Q11.4, Q12.2
!RESET: J5.3, Q2.4, R16.1, S2.1, S2.2, U3.3
!RESET1: J8.3, Q4.4, R43.1, S8.1, S8.2, U13.3
!RESET2: J13.3, Q7.4, R72.1, S12.1, S12.2, U24.3
!RESET3: J18.3, Q10.4, R101.1, S16.1, S16.2, U35.3
BST: C15.1, U6.P$6
BST1: C45.1, U18.P$6
BST2: C71.1, U29.P$6
BST3: C97.1, U40.P$6
CH340-RX: U3.35, U4.3
CH340-RX1: U13.35, U14.3
CH340-RX2: U24.35, U25.3
CH340-RX3: U35.35, U36.3
CH340-TX: U3.34, U4.2
CH340-TX1: U13.34, U14.2
CH340-TX2: U24.34, U25.2
CH340-TX3: U35.34, U36.2
D: D5.A, DIAG.1
D1: D3.A, DIAG1.1
D2: D11.A, DIAG2.1
D3: D16.A, DIAG3.1
D+: J1.A6, J1.B6, U4.5, U5.4
D+1: J3.A6, J3.B6, U14.5, U15.4
D+2: J11.A6, J11.B6, U25.5, U26.4
D+3: J16.A6, J16.B6, U36.5, U37.4
D-: J1.A7, J1.B7, U4.6, U5.6
D-1: J3.A7, J3.B7, U14.6, U15.6
D-2: J11.A7, J11.B7, U25.6, U26.6
D-3: J16.A7, J16.B7, U36.6, U37.6
DTR: Q2.1, R2.2, U4.13
DTR1: Q4.1, R41.2, U14.13
DTR2: Q7.1, R70.2, U25.13
DTR3: Q10.1, R99.2, U36.13
ESP_0/QPWR: J5.2, Q2.6, S1.1, S1.2, U3.25
ESP_0/QPWR1: J8.2, Q4.6, S7.1, S7.2, U13.25
ESP_0/QPWR2: J13.2, Q7.6, S11.1, S11.2, U24.25
ESP_0/QPWR3: J18.2, Q10.6, S15.1, S15.2, U35.25
ESP_2/RGB_DI: J5.6, STAT.DI, TP1.1, U3.24
ESP_2/RGB_DI1: J8.6, STAT1.DI, TP27.1, U13.24
ESP_2/RGB_DI2: J13.6, STAT2.DI, TP42.1, U24.24
ESP_2/RGB_DI3: J18.6, STAT3.DI, TP57.1, U35.24
ESP_4/!INT_MAG: J5.5, R28.1, U3.26, U8.5
ESP_4/!INT_MAG1: J8.5, R45.1, U13.26, U16.5
ESP_4/!INT_MAG2: J13.5, R74.1, U24.26, U27.5
ESP_4/!INT_MAG3: J18.5, R103.1, U35.26, U38.5
ESP_5/!STDBY: !STBY.2, U1.11, U3.29
ESP_5/!STDBY1: !STBY1.2, U12.11, U13.29
ESP_5/!STDBY2: !STBY2.2, U23.11, U24.29
ESP_5/!STDBY3: !STBY3.2, U34.11, U35.29
ESP_12/GPIO1: J4.8, U3.14
ESP_12/GPIO2: J6.8, U13.14
ESP_12/GPIO3: J12.8, U24.14
ESP_12/GPIO4: J17.8, U35.14
ESP_13/AUX1: J8.8, S6.1, S6.2, U13.16
ESP_13/AUX2: J5.8, S4.1, S4.2, U3.16
ESP_13/AUX3: J13.8, S10.1, S10.2, U24.16
ESP_13/AUX4: J18.8, S14.1, S14.2, U35.16
ESP_14/AUX1: J5.7, S3.1, S3.2, U3.13
ESP_14/AUX2: J8.7, S5.1, S5.2, U13.13
ESP_14/AUX3: J13.7, S9.1, S9.2, U24.13
ESP_14/AUX4: J18.7, S13.1, S13.2, U35.13
ESP_15/GPIO1: J6.7, U13.23
ESP_15/GPIO2: J12.7, U24.23
ESP_15/GPIO3: J17.7, U35.23
ESP_15/GPIO4: J4.7, U3.23
ESP_16/UH: R12.2, TP3.1, U1.3, U3.27
ESP_16/UH1: R29.2, TP17.1, U12.3, U13.27
ESP_16/UH2: R61.2, TP32.1, U23.3, U24.27
ESP_16/UH3: R90.2, TP47.1, U34.3, U35.27
ESP_17/UL: R11.2, TP4.1, U1.6, U3.28
ESP_17/UL1: R25.2, TP18.1, U12.6, U13.28
ESP_17/UL2: R60.2, TP33.1, U23.6, U24.28
ESP_17/UL3: R89.2, TP48.1, U34.6, U35.28
ESP_18/VH: R10.2, TP5.1, U1.4, U3.30
ESP_18/VH1: R23.2, TP19.1, U12.4, U13.30
ESP_18/VH2: R59.2, TP34.1, U23.4, U24.30
ESP_18/VH3: R88.2, TP49.1, U34.4, U35.30
ESP_19/WH: R8.2, TP7.1, U1.5, U3.31
ESP_19/WH1: R39.2, TP21.1, U12.5, U13.31
ESP_19/WH2: R68.2, TP36.1, U23.5, U24.31
ESP_19/WH3: R97.2, TP51.1, U34.5, U35.31
ESP_21/TP_SDA: J4.3, J7.3, R27.1, U3.33, U8.6
ESP_21/TP_SDA1: J6.3, J9.3, R51.1, U13.33, U16.6
ESP_21/TP_SDA2: J12.3, J14.3, R80.1, U24.33, U27.6
ESP_21/TP_SDA3: J17.3, J19.3, R109.1, U35.33, U38.6
ESP_22/TP_SCL: J4.2, J7.4, R26.1, U3.36, U8.1
ESP_22/TP_SCL1: J6.2, J9.4, R50.1, U13.36, U16.1
ESP_22/TP_SCL2: J12.2, J14.4, R79.1, U24.36, U27.1
ESP_22/TP_SCL3: J17.2, J19.4, R108.1, U35.36, U38.1
ESP_23/VL: R9.2, TP6.1, U1.10, U3.37
ESP_23/VL1: R40.2, TP20.1, U12.10, U13.37
ESP_23/VL2: R69.2, TP35.1, U23.10, U24.37
ESP_23/VL3: R98.2, TP50.1, U34.10, U35.37
ESP_25/TP_A1: J4.6, U3.10
ESP_25/TP_A2: J6.6, U13.10
ESP_25/TP_A3: J12.6, U24.10
ESP_25/TP_A4: J17.6, U35.10
ESP_26/TP_A0: J4.5, U3.11
ESP_26/TP_A1: J6.5, U13.11
ESP_26/TP_A2: J12.5, U24.11
ESP_26/TP_A3: J17.5, U35.11
ESP_27/GPIO1: J6.4, U13.12
ESP_27/GPIO2: J4.4, U3.12
ESP_27/GPIO3: J12.4, U24.12
ESP_27/GPIO4: J17.4, U35.12
ESP_32/CURR_SENSE: J5.4, R21.2, TP9.1, U3.8, U9.1
ESP_32/CURR_SENSE1: J8.4, R58.2, TP23.1, U13.8, U22.1
ESP_32/CURR_SENSE2: J13.4, R87.2, TP38.1, U24.8, U33.1
ESP_32/CURR_SENSE3: J18.4, R116.2, TP53.1, U35.8, U44.1
ESP_33/WL: R7.2, TP8.1, U1.7, U3.9
ESP_33/WL1: R38.2, TP22.1, U12.7, U13.9
ESP_33/WL2: R67.2, TP37.1, U23.7, U24.9
ESP_33/WL3: R96.2, TP52.1, U34.7, U35.9
ESP_34/DIAG: DIAG.2, U1.12, U3.6
ESP_34/DIAG1: DIAG1.2, U12.12, U13.6
ESP_34/DIAG2: DIAG2.2, U23.12, U24.6
ESP_34/DIAG3: DIAG3.2, U34.12, U35.6
ESP_35/U_OUT: TP10.1, U3.7, U7.5
ESP_35/U_OUT1: TP24.1, U13.7, U19.5
ESP_35/U_OUT2: TP39.1, U24.7, U30.5
ESP_35/U_OUT3: TP54.1, U35.7, U41.5
ESP_36/V_OUT: TP11.1, U3.4, U11.5
ESP_36/V_OUT1: TP25.1, U13.4, U21.5
ESP_36/V_OUT2: TP40.1, U24.4, U32.5
ESP_36/V_OUT3: TP55.1, U35.4, U43.5
ESP_39/W_OUT: TP12.1, U3.5, U10.5
ESP_39/W_OUT1: TP26.1, U13.5, U20.5
ESP_39/W_OUT2: TP41.1, U24.5, U31.5
ESP_39/W_OUT3: TP56.1, U35.5, U42.5
FB: C16.1, R5.1, R6.2, U6.P$3
FB1: C46.1, R54.1, R55.2, U18.P$3
FB2: C72.1, R83.1, R84.2, U29.P$3
FB3: C98.1, R112.1, R113.2, U40.P$3
GND: C1.2, C3.2, C4.2, C5.2, C6.2, C7.-, C8.2, C9.2, C10.2, C11.2, C12.2, C13.2, C14.2, C17.2, C18.2, C19.2, C20.2, C21.2, C22.2, C23.2, C24.2, C25.2, C26.2, D1.C, D2.C, D7.A, J1.GND, J1.GND2, J2.1, J4.1, J7.1, R1.1, R4.1, R6.1, R7.1, R8.1, R9.1, R10.1, R11.1, R12.1, R13.1, R14.1, R15.1, R18.1, R19.1, R20.1, S1.3, S1.4, S2.3, S2.4, S3.3, S3.4, S4.3, S4.4, SHLD.1, STAT.GND, U1.8, U1.9, U1.14, U1.PAD, U2.2, U3.1, U3.15, U3.38, U3.GND, U3.GNDT1, U3.GNDT2, U3.GNDT3, U3.GNDT4, U3.GNDT5, U3.GNDT6, U3.GNDT7, U3.GNDT8, U4.1, U5.2, U6.P$4, U6.P$8, U7.2, U7.4, U7.7, U8.2, U8.3, U9.2, U10.2, U10.4, U10.7, U11.2, U11.4, U11.7
GND1: C27.2, C28.2, C29.2, C31.2, C32.2, C33.2, C34.2, C35.2, C36.2, C37.2, C38.-, C39.2, C40.2, C41.2, C42.2, C43.2, C44.2, C47.2, C48.2, C49.2, C50.2, C51.2, C52.2, D6.A, D9.C, D10.C, J3.GND, J3.GND2, J6.1, J9.1, J10.1, R23.1, R25.1, R29.1, R30.1, R31.1, R35.1, R36.1, R37.1, R38.1, R39.1, R40.1, R52.1, R53.1, R55.1, R57.1, S5.3, S5.4, S6.3, S6.4, S7.3, S7.4, S8.3, S8.4, SHLD1.1, STAT1.GND, U12.8, U12.9, U12.14, U12.PAD, U13.1, U13.15, U13.38, U13.GND, U13.GNDT1, U13.GNDT2, U13.GNDT3, U13.GNDT4, U13.GNDT5, U13.GNDT6, U13.GNDT7, U13.GNDT8, U14.1, U15.2, U16.2, U16.3, U17.2, U18.P$4, U18.P$8, U19.2, U19.4, U19.7, U20.2, U20.4, U20.7, U21.2, U21.4, U21.7, U22.2
GND2: C53.2, C54.2, C55.2, C57.2, C58.2, C59.2, C60.2, C61.2, C62.2, C63.2, C64.-, C65.2, C66.2, C67.2, C68.2, C69.2, C70.2, C73.2, C74.2, C75.2, C76.2, C77.2, C78.2, D12.A, D14.C, D15.C, J11.GND, J11.GND2, J12.1, J14.1, J15.1, R59.1, R60.1, R61.1, R62.1, R63.1, R64.1, R65.1, R66.1, R67.1, R68.1, R69.1, R81.1, R82.1, R84.1, R86.1, S9.3, S9.4, S10.3, S10.4, S11.3, S11.4, S12.3, S12.4, SHLD2.1, STAT2.GND, U23.8, U23.9, U23.14, U23.PAD, U24.1, U24.15, U24.38, U24.GND, U24.GNDT1, U24.GNDT2, U24.GNDT3, U24.GNDT4, U24.GNDT5, U24.GNDT6, U24.GNDT7, U24.GNDT8, U25.1, U26.2, U27.2, U27.3, U28.2, U29.P$4, U29.P$8, U30.2, U30.4, U30.7, U31.2, U31.4, U31.7, U32.2, U32.4, U32.7, U33.2
GND3: C79.2, C80.2, C81.2, C83.2, C84.2, C85.2, C86.2, C87.2, C88.2, C89.2, C90.-, C91.2, C92.2, C93.2, C94.2, C95.2, C96.2, C99.2, C100.2, C101.2, C102.2, C103.2, C104.2, D17.A, D19.C, D20.C, J16.GND, J16.GND2, J17.1, J19.1, J20.1, R88.1, R89.1, R90.1, R91.1, R92.1, R93.1, R94.1, R95.1, R96.1, R97.1, R98.1, R110.1, R111.1, R113.1, R115.1, S13.3, S13.4, S14.3, S14.4, S15.3, S15.4, S16.3, S16.4, SHLD3.1, STAT3.GND, U34.8, U34.9, U34.14, U34.PAD, U35.1, U35.15, U35.38, U35.GND, U35.GNDT1, U35.GNDT2, U35.GNDT3, U35.GNDT4, U35.GNDT5, U35.GNDT6, U35.GNDT7, U35.GNDT8, U36.1, U37.2, U38.2, U38.3, U39.2, U40.P$4, U40.P$8, U41.2, U41.4, U41.7, U42.2, U42.4, U42.7, U43.2, U43.4, U43.7, U44.2
MOTOR_EN: J5.1, U6.P$2
MOTOR_EN1: J8.1, U18.P$2
MOTOR_EN2: J13.1, U29.P$2
MOTOR_EN3: J18.1, U40.P$2
unnamed: J1.A5, R19.2
unnamed: C5.1, U4.4
unnamed: J1.B5, R18.2
unnamed: C2.2, U1.2
unnamed: D8.C, R30.2
unnamed: R24.1, U2.3
unnamed: Q2.5, R2.1
unnamed: Q2.2, R3.1
unnamed: D2.A, R17.1
unnamed: D3.C, R35.2
unnamed: INT.1, R28.2
unnamed: I2C.3, R26.2
unnamed: I2C.1, R27.2
unnamed: R20.2, R21.1, U9.4
unnamed: PWR.1, R17.2
unnamed: J3.A5, R37.2
unnamed: BYP.1, C11.1, F1.1, MEAS.2, MEAS.4
unnamed: J3.B5, R36.2
unnamed: C30.2, U12.2
unnamed: Q4.5, R41.1
unnamed: Q1.3, Q3.1, R4.2
unnamed: Q1.1, Q1.2, Q1.5, R1.2
unnamed: Q4.2, R42.1
unnamed: INT1.1, R45.2
unnamed: D9.A, R49.1
unnamed: D1.A, R22.1
unnamed: MPWR.1, R22.2
unnamed: PWR1.1, R49.2
unnamed: D4.C, R13.2
unnamed: R44.1, U17.3
unnamed: C39.1, U14.4
unnamed: I2C1.3, R50.2
unnamed: D5.C, R15.2
unnamed: I2C1.1, R51.2
unnamed: BYP1.1, C41.1, F2.1, MEAS1.2, MEAS1.4
unnamed: Q5.3, Q6.1, R53.2
unnamed: Q5.1, Q5.2, Q5.5, R52.2
unnamed: D10.A, R56.1
unnamed: MPWR1.1, R56.2
unnamed: R57.2, R58.1, U22.4
unnamed: D13.C, R62.2
unnamed: D11.C, R64.2
unnamed: J11.A5, R66.2
unnamed: J11.B5, R65.2
unnamed: C56.2, U23.2
unnamed: Q7.5, R70.1
unnamed: Q7.2, R71.1
unnamed: INT2.1, R74.2
unnamed: D14.A, R78.1
unnamed: PWR2.1, R78.2
unnamed: R73.1, U28.3
unnamed: C65.1, U25.4
unnamed: I2C2.3, R79.2
unnamed: I2C2.1, R80.2
unnamed: BYP2.1, C67.1, F3.1, MEAS2.2, MEAS2.4
unnamed: Q8.3, Q9.1, R82.2
unnamed: Q8.1, Q8.2, Q8.5, R81.2
unnamed: D15.A, R85.1
unnamed: MPWR2.1, R85.2
unnamed: R86.2, R87.1, U33.4
unnamed: D18.C, R91.2
unnamed: D16.C, R93.2
unnamed: J16.A5, R95.2
unnamed: J16.B5, R94.2
unnamed: C82.2, U34.2
unnamed: Q10.5, R99.1
unnamed: Q10.2, R100.1
unnamed: INT3.1, R103.2
unnamed: D19.A, R107.1
unnamed: PWR3.1, R107.2
unnamed: R102.1, U39.3
unnamed: C91.1, U36.4
unnamed: I2C3.3, R108.2
unnamed: I2C3.1, R109.2
unnamed: BYP3.1, C93.1, F4.1, MEAS3.2, MEAS3.4
unnamed: Q11.3, Q12.1, R111.2
unnamed: Q11.1, Q11.2, Q11.5, R110.2
unnamed: D20.A, R114.1
unnamed: MPWR3.1, R114.2
unnamed: R115.2, R116.1, U44.4
RTS: Q2.3, R3.2, U4.14
RTS1: Q4.3, R42.2, U14.14
RTS2: Q7.3, R71.2, U25.14
RTS3: Q10.3, R100.2, U36.14
S: !STBY.1, D4.A
S1: !STBY1.1, D8.A
S2: !STBY2.1, D13.A
S3: !STBY3.1, D18.A
SENSE: R14.2, U1.16, U1.20, U9.3
SENSE1: R31.2, U12.16, U12.20, U22.3
SENSE2: R63.2, U23.16, U23.20, U33.3
SENSE3: R92.2, U34.16, U34.20, U44.3
SENSE_U: R32.1, U1.15, U7.8
SENSE_U1: R46.1, U12.15, U19.8
SENSE_U2: R75.1, U23.15, U30.8
SENSE_U3: R104.1, U34.15, U41.8
SENSE_V: R33.1, U1.17, U11.8
SENSE_V1: R47.1, U12.17, U21.8
SENSE_V2: R76.1, U23.17, U32.8
SENSE_V3: R105.1, U34.17, U43.8
SENSE_W: R34.1, U1.1, U10.8
SENSE_W1: R48.1, U12.1, U20.8
SENSE_W2: R77.1, U23.1, U31.8
SENSE_W3: R106.1, U34.1, U42.8
SHLD: J1.SHLD1, J1.SHLD2, J1.SHLD3, J1.SHLD4, SHLD.2
SHLD1: J3.SHLD1, J3.SHLD2, J3.SHLD3, J3.SHLD4, SHLD1.2
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

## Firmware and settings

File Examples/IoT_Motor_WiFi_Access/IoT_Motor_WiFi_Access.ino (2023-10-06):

/*
  Steps:
  1. Connect to the access point "yourAp"
  2. Point your web browser to http://192.168.4.1/H to turn the motor on or http://192.168.4.1/L to turn it off
     OR
     Run raw TCP "GET /H" and "GET /L" on PuTTY terminal with 192.168.4.1 as IP address and 80 as port

  Original WiFi Code created for arduino-esp32 on 04 July, 2018
  by Elochukwu Ifediora (fedy0)
*/

#include <WiFi.h>
#include <WiFiClient.h>
#include <WiFiAP.h>

// To download the Arduino Simple FOC Library, use this link: https://docs.simplefoc.com/arduino_simplefoc_library_showcase
#include <SimpleFOC.h> 

// Set these to your desired credentials.
const char *ssid = "ESP32IoTMotorDriver";
const char *password = "your-password"; // Make sure the new password set is at least 7 characters

WiFiServer server(80);

// BLDC motor & driver instance
BLDCMotor motor = BLDCMotor(8);

// BLDCDriver6PWM(int phA_h,int phA_l,int phB_h,int phB_l,int phC_h,int phC_l, int en)
BLDCDriver6PWM driver = BLDCDriver6PWM(16,17, 18,23, 19,33, 34);

//target variable in rad/s (radians per second)
float target_velocity_rps = 3;

// instantiate the commander
Commander command = Commander(Serial);
void doTarget(char* cmd) { command.scalar(&target_velocity_rps, cmd); }
void doLimit(char* cmd) { command.scalar(&motor.voltage_limit, cmd); }



void setup() {
  Serial.begin(115200);

  // Begin example of the magnetic sensor code
  Serial.println("Example: Communication over WiFi with the IoT Motor Driver");

  Serial.println();
  Serial.println("Configuring access point...");

  // ********* WiFi config *********
  // You can remove the password parameter if you want the AP to be open.
  // a valid password must have more than 7 characters
  if (!WiFi.softAP(ssid, password)) {
    log_e("Soft AP creation failed.");
    while(1);
  }
  IPAddress myIP = WiFi.softAPIP();
  Serial.print("AP IP address: ");
  Serial.println(myIP);
  server.begin();

  Serial.println("Server started");

  // ********* Driver config *********
  // power supply voltage [V]
  driver.voltage_power_supply = 3.3; // ESP32 3.3V supply pin
  // PWM Configuration
  driver.pwm_frequency = 20000;
  // this value is fixed on startup
  driver.voltage_limit = 4;
  driver.init();
  // link the motor and the driver to enable usage
  motor.linkDriver(&driver);
  // limit the voltage to be set to the motor
  motor.voltage_limit = 4;   // [V]
  // open loop control config
  motor.controller = MotionControlType::velocity_openloop;
  // init motor hardware
  motor.init();
 
  // add target command T
  command.add('T', doTarget, "target velocity");
  command.add('L', doLimit, "voltage limit");

  Serial.println("Motor ready!");
  Serial.print("Set target velocity [rad/s]: ");
  Serial.println(target_velocity_rps);
  _delay(1000);


}

void loop() 
{
  // Basic motor movement
  motor.move(target_velocity_rps);
  // user communication to motor
  command.run();

  WiFiClient client = server.available();   // listen for incoming clients

  if (client) {                             // if you get a client,
    Serial.println("New Client.");           // print a message out the serial port
    String currentLine = "";                // make a String to hold incoming data from the client
    while (client.connected()) {            // loop while the client's connected
      if (client.available()) {             // if there's bytes to read from the client,
        char c = client.read();             // read a byte, then
        Serial.write(c);                    // print it out the serial monitor
        if (c == '\n') {                    // if the byte is a newline character

          // if the current line is blank, you got two newline characters in a row.
          // that's the end of the client HTTP request, so send a response:
          if (currentLine.length() == 0) {
            // HTTP headers always start with a response code (e.g. HTTP/1.1 200 OK)
            // and a content-type so the client knows what's coming, then a blank line:
            client.println("HTTP/1.1 200 OK");
            client.println("Content-type:text/html");
            client.println();

            // the content of the HTTP response follows the header:
            client.print("Click <a href=\"/H\">here</a> to turn ON the motor.<br>");
            client.print("Click <a href=\"/L\">here</a> to turn OFF the motor.<br>");

            // The HTTP response ends with another blank line:
            client.println();
            // break out of the while loop:
            break;
          } else {    // if you got a newline, then clear currentLine:
            currentLine = "";
          }
        } else if (c != '\r') {  // if you got anything else but a carriage return character,
          currentLine += c;      // add it to the end of the currentLine
        }

        // Check to see if the client request was "GET /H" or "GET /L":
        if (currentLine.endsWith("GET /H")) {
          target_velocity_rps = 3;
        }
        if (currentLine.endsWith("GET /L")) {
          target_velocity_rps = 0;
        }
      }
    }
    // close the connection:
    client.stop();
    Serial.println("Client Disconnected.");
  }
}

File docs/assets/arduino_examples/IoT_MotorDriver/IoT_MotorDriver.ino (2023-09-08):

/******************************************************************************
	IoT Motor Driver Example

	Written By:
		Madison Chodikov
		Eric Orosel
	Company: SparkFun Electronics	
	Date: September 1 2023

	This sketch is a stripped down version of the firmware that is preprogrammed
	on the IoT Motor Driver. It is based on the open loop, velocity motor control
	example from the SimpleFOC Arduino library.

	This sketch will spin the motor based on the button inputs:
		- Button 13: Starts/Stops the motor rotation
		- Button 14: When spinning, switches the direction of rotation

===============================================================================
	Products:
		IoT Brushless Motor Driver: https://www.sparkfun.com/products/22132

	Repository:
		https://github.com/sparkfun/SparkFun_IoT_Brushless_Motor_Driver
===============================================================================

	SparkFun code, firmware, and software is released under the MIT 
	License	(http://opensource.org/licenses/MIT).

	Distributed as-is; no warranty is given.
******************************************************************************/

#include <Wire.h>
#include <SimpleFOC.h> //http://librarymanager/All#Simple%20FOC


//GPIO
#define auxBtn2   13
#define auxBtn1   14  

//driver
#define uh16      16
#define ul17      17
#define vh18      18
#define wh19      19
#define vl23      23
#define wl33      33
#define curSense  32

bool state = true;

//motor driver
BLDCMotor motor = BLDCMotor(7);
BLDCDriver6PWM driver = BLDCDriver6PWM(uh16, ul17, vh18, vl23, wh19, wl33,  curSense);
float target_velocity = 0.0;
Commander command = Commander(Serial);
void doTarget(char* cmd) { command.scalar(&target_velocity, cmd); }
void doLimit(char* cmd) { command.scalar(&motor.voltage_limit, cmd); }

//////////////////////motor demo stuff///////////////////////////
struct Button{
  const uint8_t PIN;
  uint32_t numberKeyPresses;
  bool pressed;
};
Button aux1 = {auxBtn1, 0, false};
Button aux2 = {auxBtn2, 0, false};

void IRAM_ATTR isr1(){
  aux1.pressed = true;
  target_velocity = target_velocity*(-1);
  Serial.println("Changing directions.. ");
}

void IRAM_ATTR isr2(){
  aux2.numberKeyPresses++;
  aux2.pressed = true;
  
  if((aux2.numberKeyPresses % 2) == 0)
  {
    target_velocity = 0;
    Serial.println("Stopping motor.. ");
  }
  else
  {
    target_velocity = 5;
    motor.enable();
    Serial.println("Starting motor.. ");
  }
}


void setup() {

  //motor demo stuff
  driver.voltage_power_supply = 3.3;
  driver.pwm_frequency = 20000;
  driver.voltage_limit = 4;
  driver.init();
  motor.linkDriver(&driver);
  motor.voltage_limit = 4;
  motor.controller = MotionControlType::velocity_openloop;
  motor.init();
  motor.disable();
  pinMode(aux1.PIN, INPUT_PULLUP); // Sets pin 14 on the ESP32 as an interrupt
  attachInterrupt(aux1.PIN, isr1, FALLING); // Triggers when aux1 is pulled to GND (button pressed)
  pinMode(aux2.PIN, INPUT_PULLUP); // Sets pin 13 on the ESP32 as an interrupt
  attachInterrupt(aux2.PIN, isr2, FALLING); // Triggers when aux2 is pulled to GND (button pressed)
  delay(100);

  Serial.begin(115200);
}

/////////////////////////////////////////////////////////////////////////
void loop() { 

  // Button Press ISR
  if(aux1.pressed){ 
    aux1.pressed = false;
  }
  
  // Turning motor on and off
  if(aux2.pressed){ 
    aux2.pressed = false;
  }

  // open loop velocity movement
  // using motor.voltage_limit and motor.velocity_limit
  // Basic motor movement
  motor.move(target_velocity);

  // user communication
  command.run();

  delay(5);
}

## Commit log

2023-02-23 Design updates
    Deleted unneeded files folders, continued with designing schematic
    [ESP32_BLDC_Motor_Driver.sch]
2023-02-23 Updates to schematic, added new part
    Continued work with schematic, added more parts to the project/library (TMC6300, output connector for motor, ESP32)
    [ESP32_BLDC_Motor_Driver.sch]
2023-02-27 Added datasheet, further schematic work
    Added datasheet for an IC and continued work on schematic. All sections should now be on the project, need to be checked and completed.
    [ESP32_BLDC_Motor_Driver.sch]
2023-02-28 Design updates
    Committing updates from the day - need much much more work
    [ESP32_BLDC_Motor_Driver.sch]
2023-03-03 Design updates and addition of datasheet
    Added datasheet for new IC on board, continued with design
    [ESP32_BLDC_Motor_Driver.sch]
2023-03-07 Added correct datasheet, continued design
    Continued with design of board, nearing finish of schematic design
    [ESP32_BLDC_Motor_Driver.sch]
2023-03-14 Schematic ready for review
    The schematic has been looked over and is ready for review before starting on the layout. Added Sparkle part number to new library component, added datasheet for new component on board
    [ESP32_BLDC_Motor_Driver.sch]
2023-03-14 Design Updates
    Created new board file, added output connector to motor output in case users want to use a different motor for this board
    [ESP32_BLDC_Motor_Driver.brd, ESP32_BLDC_Motor_Driver.sch]
2023-03-15 Design Review Updates
    Organized file folders, updates from design review - see document for full list of changes. Still needs a little more work before starting fully on the board file
    [ESP32_BLDC_Motor_Driver.brd, ESP32_BLDC_Motor_Driver.sch]
2023-03-16 Added datasheet, further changes from schematic review
    See schematic review for more detailed changes: updated 3.3V LDO for an actual LDO, finished auto-reset circuitry, fixed pinout connections to breakout headers, changed size of logo, added qwiic logo, continued with layout. Datasheet added for the 3.3V LDO chosen.
    [ESP32_BLDC_Motor_Driver.brd, ESP32_BLDC_Motor_Driver.sch]
2023-03-21 Continue with design
    Adjusted schematic components for better routing. Continued routing design - still a lot left to complete.
    [ESP32_BLDC_Motor_Driver.brd, ESP32_BLDC_Motor_Driver.sch]
2023-03-21 Continued work on layout
    Added polygons to layout, added layers 2,15, continued with routing
    [ESP32_BLDC_Motor_Driver.brd, ESP32_BLDC_Motor_Driver.sch]
2023-03-24 Added new component
    Added library component and datasheet for the magnetic encoder.
2023-03-28 Updates to library and schematic
    Added decoupling caps to ESP32 as per the datasheet, updated the library for the magnetic encoder for better schematic routing, moved components on the board for layout, made small changes/fixes to schematic for net label names and for the breakout header
    [ESP32_BLDC_Motor_Driver.brd, ESP32_BLDC_Motor_Driver.sch]
2023-04-05 Design updates for board and schematic
    Continued work from schematic and layout - not complete, needs more routing and placement adjustments.
    [ESP32_BLDC_Motor_Driver.brd, ESP32_BLDC_Motor_Driver.sch]
2023-04-05 Addition of motor footprint to library; updates to schematic and layout
    Opened up layout of the board for addition of milling layer; broke out power good signal to the breakout headers; adjusted auxilary buttons for proper use; adjusted VIO to be configured correctly; changed note for copper weight usage; created footprint for the motor
    [ESP32_BLDC_Motor_Driver.brd, ESP32_BLDC_Motor_Driver.sch]
2023-04-10 Layout Updates
    Completed all air wires and most design rule errors - still a few to go. Layout primarily solidified. logos, name, and labels added to board.
    [ESP32_BLDC_Motor_Driver.brd, ESP32_BLDC_Motor_Driver.sch]
2023-04-18 Design Updates
    Further work done on inline current sensing - restarting computer
    [ESP32_BLDC_Motor_Driver.brd, ESP32_BLDC_Motor_Driver.sch]
2023-04-19 Updates to schematic and layout as per design review checklist
    Finished design errors- close to design review
    [ESP32_BLDC_Motor_Driver.brd, ESP32_BLDC_Motor_Driver.sch]
2023-04-19 Updates for Design Review
    Added more silk for buttons and outputs; added datasheet for correct Op Amp and deleted the old one; adjusted MOLEX output connector to motor for better connectivity and less strain on the cable; changed version number to v01; added more GND vias
    [ESP32_BLDC_Motor_Driver.brd, ESP32_BLDC_Motor_Driver.sch]
2023-04-21 Design Updates from design review - schematic changes mostly
    ***Changes are still not done*** Changes can be seen detailed in the protos design review; changed TMAG5273 symbol to be correct
    [ESP32_BLDC_Motor_Driver.brd, ESP32_BLDC_Motor_Driver.sch]
2023-04-26 Updates for design review
    Fixed schematic - reordering ESP_32 pinouts, breakout headers, adjusted inline current sensing; re-completed layout - repositioned placement of power scheme and input connectors, swapped placement of motor and motor driver/current sensors; fixed screw hole size of the motor; fixed schematic symbol for hall effect sensor.
    For a full list, see design review document
    [ESP32_BLDC_Motor_Driver.brd, ESP32_BLDC_Motor_Driver.sch]
2023-04-28 Design review changes
    Updated datasheets with correct parts in it now; removed power jack; changed direction of motor and output connector to the motor; swapped resistances of op amp for inline current sensing; updated sizes of some resistances; fixed power scheme of the board; added perfect diode circuit; for more information, see protos review doc
    [ESP32_BLDC_Motor_Driver.brd, ESP32_BLDC_Motor_Driver.sch]
2023-05-01 Design Review Changes
    Added back in AP63557 circuit for more power to motor; Adjusted trace size for better differential pairs and power usage; created standoff board for the motor to sit on while moving; see design notes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
    [ESP32_BLDC_Motor_Driver.brd, ESP32_BLDC_Motor_Driver.sch, IoT_Motor_Driver_Standoff.brd]
2023-05-01 Final design changes made; files for ordering added
    Made final adjustments with Alex - check document for more information on small adjustments; ran CAM script for output files for board; also made output CAM files for standoff to be ordered as well.
    [ESP32_BLDC_Motor_Driver.GBL, ESP32_BLDC_Motor_Driver.GBO, ESP32_BLDC_Motor_Driver.GBP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]
2023-06-08 V10 INITIAL COMMIT
    Added datasheets for new parts; created new library component for the INA240 inline current sensing; lined up other parts for symmetry; redid the OPA344 current sensing section
    [ESP32_BLDC_Motor_Driver.brd, ESP32_BLDC_Motor_Driver.sch, OpAmpTest.sch]
2023-06-08 Standoff Updates
    Changed the width of the circle for the standoff so there is no friction on the motor when it is spinning. Continued work with layout.
    [ESP32_BLDC_Motor_Driver.brd, IoT_Motor_Driver_Standoff.brd]
2023-06-09 Reds Review - final changes
    Deleted datasheets no longer needed; updated documents to parts currently on board; added more GND vias to GND return paths on the layout; Fixed the OPA344 op amp section; added decoupling caps to the current sense op amp and the inline current sense op amps; turned the motor and updated the silk to be correct; adjusted the output connector to the motor to be further away leaving less extra wire; panelized board files for production/ordering review; changed the part INA240A1 to have pinout consistent with other components in the SparkFun library; Added more test points for the output to the motor;
    [ESP32_BLDC_Motor_Driver-Panel.GBL, ESP32_BLDC_Motor_Driver-Panel.GBO, ESP32_BLDC_Motor_Driver-Panel.GBP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]
2023-06-14 Changes from Reds Review
    Fixed INA240A1 symbol; changed voltage input range; adjusted OPA344 to be non-inverting; SENSE trace now 30mil instead of 15mil; moved inline current sense resistors to allow kelvin connections; moved connector down and turned motor to allow better polygon connections for U; Reworked 3.3V power distribution with Op Amps and changed caps to be on power pin rather than reference; changed some silk names; turned thermals off.
    [ESP32_BLDC_Motor_Driver.brd, ESP32_BLDC_Motor_Driver.sch]
2023-06-15 Updated files for ordering
    Completed all the final requests from the re-review after the reds review; double checked the test points to the test board; updated pcb spacers; updated files for ordering boards
    [ESP32_BLDC_Motor_Driver-Panel.GBL, ESP32_BLDC_Motor_Driver-Panel.GBO, ESP32_BLDC_Motor_Driver-Panel.GBS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]
2023-07-05 Updated with Sparkle BOM part change
    No changes to board layout has been made; only a Sparkle part change to U9 due to a retired part.
    [ESP32_BLDC_Motor_Driver.brd, ESP32_BLDC_Motor_Driver.sch]
2023-08-17 Removed uneeded files; renamed standoff to space in file folder
    Removed the op-amp testing schematic and datasheet; renamed Standoff to Spacer for less confusion with ordering/following along
    [IoT_Motor_Driver_Standoff.GBL, IoT_Motor_Driver_Standoff.GBO, IoT_Motor_Driver_Standoff.GBP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]
2023-09-08 Move production folder
    [ESP32_BLDC_Motor_Driver-Panel.GBL, ESP32_BLDC_Motor_Driver-Panel.GBO, ESP32_BLDC_Motor_Driver-Panel.GBP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]
2023-09-20 Update
    Markdown - Fix carriage return spacing
2023-10-06 Added new example folder for WiFi example
    Added WiFi example for IoT Motor Driver as per request from above
2024-07-23 Updates github action to just include the esp32 thing plus c board

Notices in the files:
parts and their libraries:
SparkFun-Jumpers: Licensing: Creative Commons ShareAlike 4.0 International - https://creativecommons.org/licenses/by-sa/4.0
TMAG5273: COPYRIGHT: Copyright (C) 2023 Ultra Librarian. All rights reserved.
